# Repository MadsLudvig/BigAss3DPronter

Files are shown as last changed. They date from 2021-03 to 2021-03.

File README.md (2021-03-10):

# Industrial 3D Printer
*__Big 3D printer made with industrial parts from an injection molding machine__*

### Introduction

This is a 3D printer made with an extruder from an injection moulding machine and Motors and axis from several old ATM CNC robots. It will be using an material dryer and a mini vacuum conveyor for supplying the extruder with material. It will be build such that the extruder only moves on one axis because of its weight (approximately 50kg). The extruder will be moved on the x-axis and the bottom plate will be moved on the z- and y-axis. The software will be Marlin which is going to run on a Teensy 4.0. Then octoprint will be used as an Marlin host to control. Here octoprint will run on a Raspberry Pi 4.0 with an 15" industrial grade touch screen.

*__More information on the individual modules can be seen in the "Modules" folder__*

### Mechanical composition

Here as said before the extruder is going to be moved in the X-axis and the bottom plate is going to be moved in the Y- and Z-axis. This is seen in Figure 5 below:

3D-Printer-Axis

*Figure 5: Here is seen an example of how the axis will look*

Here it should be noted that although the axis placements are correct on the image. The way the axisses are moved are not. This image is just to show axis placement. The Z-axis is not moving the extruder it should here be moving the bottom plate instead. The reason why the extruder is placed on the x-axis is because of its sheer size and weight. Here it will be advantagous only to move it from side to side to minimize movement of mass. To make the x-axis move the weight of the extruder, the long axis of the ATM CNC robot is going to be used. This is because this has lots of already built-in support and can therefore support the extruder with ease. It also has place for motor mounting, gear and gearrack for moving the axis, and a cable carrier. This i going to be very advantageus for running the material supply line for the extruder, motor cables for x and w axisses, and heating element wires for extruder. Everything will then be mounted on a steel frame made out of welded steel beams. The material of the bottom plate is being researched, so the best material can be found. For now the material is aluminium, but that could also be replaced with borosilicate glass because of its hardness and temperature resistance

### Global Bill of Materials

| Name | Quantity | Link | Price (DKK) |
| :--- | :---: | :---: | :---: |
| Conradt mini vacuum conveyer | 1 | | 4000 |
| ILCE-QX1 Power adapter | 1 | [Link](https://www.subtel.dk/index.php?offerId=3978956963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) | 259 |
| 15" Touch screen | 1 | [Link](https://www.beetronics.dk/15-tommer-touchskaerm-metal-4-3) | 2699 |
| Cable | 1 | [Link](https://dk.rs-online.com/web/p/yy-kabel/1811780/) | 589 |
| Connector | 16 |  [Link](https://dk.rs-online.com/web/p/d-sub-stik/5443749/)  | 6.376 |
| Connector house | 16 | [Link](https://dk.rs-online.com/web/p/d-sub-bagkapper/5444039/) | 27.22 |
| Material dryer | 1 | | NaN |
| SN74LS640N | 6 | [Link](https://www.ti.com/store/ti/en/p/product/?p=SN74LS640N) | 9.54 |
| SN74ABT245BN | 6 | [Link](https://www.ti.com/store/ti/en/p/product/?p=SN74ABT245BN) | 4.52 |
| Aluminium bottom plate | 1 | | NaN |
| Heating elements bottom plate | 1 | | NaN |
| Steel frame | 1 | | NaN |
| Mounting adapter for servo motor to extruder | 1 | | NaN |

So here the price comes up to: 8169kr. DKK for now. Here it should be noted that this is not close to the final cost, since the mounting brackets, the steel frame, and the aluminium bottom plate will cost a lot.

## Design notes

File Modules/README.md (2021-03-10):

# Module Interfacing

### Module interfacing can be seen in the diagram below

*-- Insert diagram here --*

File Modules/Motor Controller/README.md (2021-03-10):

# Motor Controller
The motors are controlled by lenze servo controllers. All of the servo drives and the power management are already packed in a nice cabinet. This will be reused. Here the teensy will be sitting inside this cabinet. The model of the servo controllers is Lenze 9300. Here the X9 and X10 connectors will be used as seen here:

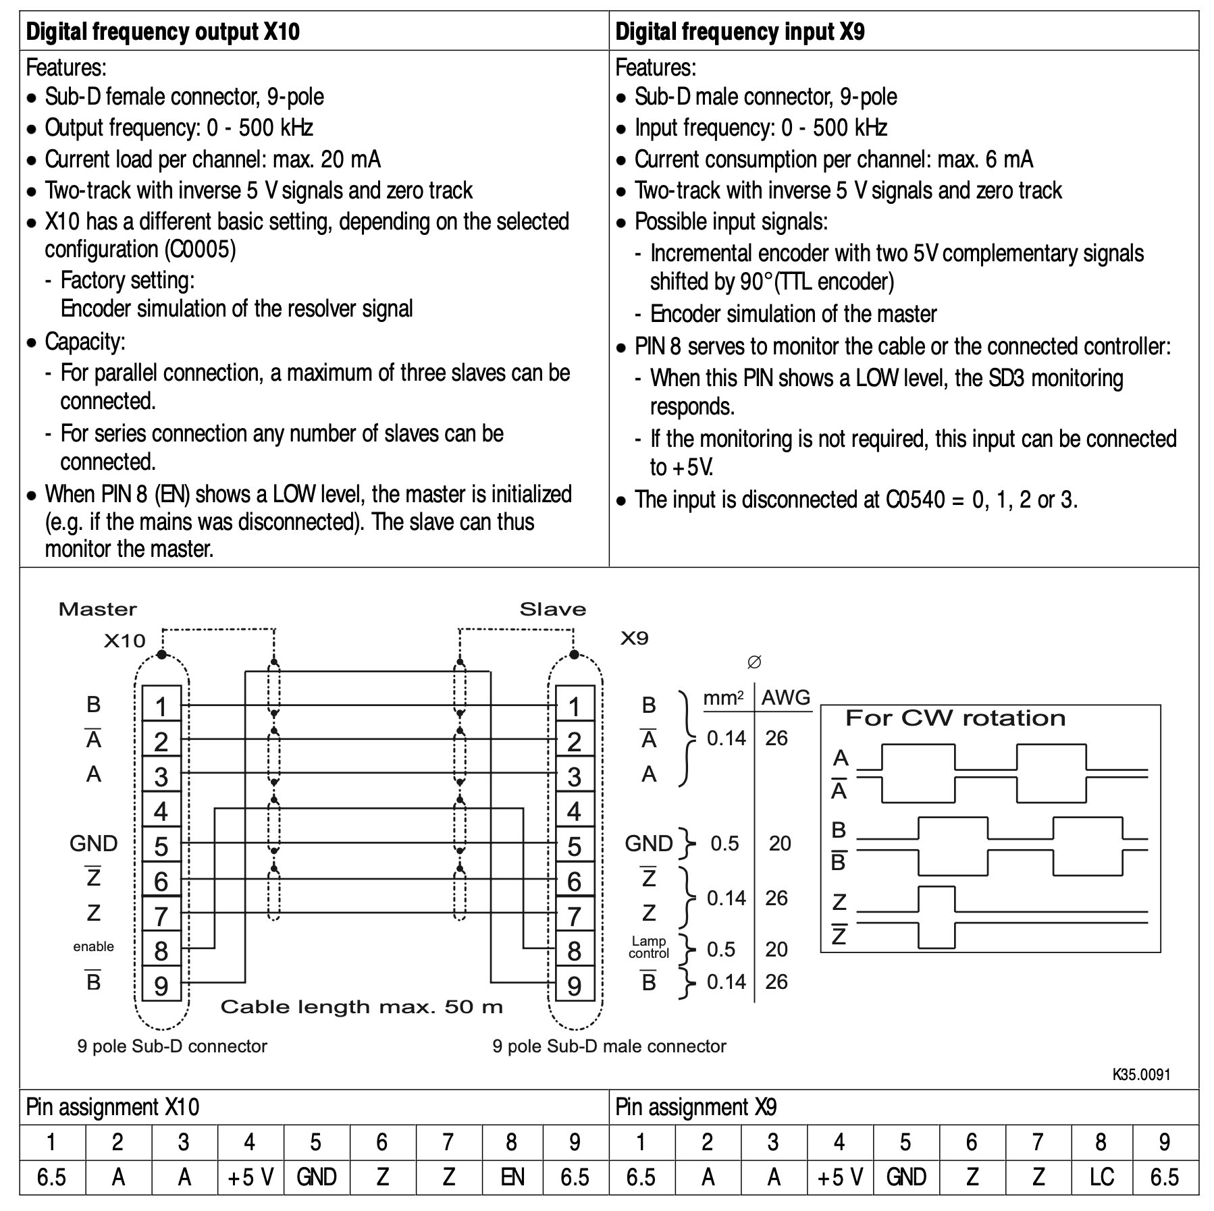
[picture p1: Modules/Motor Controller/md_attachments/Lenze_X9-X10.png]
Lenze X9-X10


*Figure 1: Page 47 of lenze 9300 servodrive manual*

*__Lenze manual:  [BA_9300_Register_control_EN.pdf](/md_attachments/BA_9300_Register_control_EN.pdf)__*

Here the X9 connector is digital frequency input. This input requires a TTL encoder signal. Then the servo drive will mimic this encoder signal. This way the drive can be controlled. So the Teensy 4.0 will input the Marlin stepper signals to this input. The plan is to have 4 outputs on the teensy that, so the X,Y,Z,W axisses can be controlled. Here the W axis is the motor that turns the extruder. Another nice feature this allows is that the servo drives can easily be daisy chained if multiple motors is needed per axis by connecting the X10 and X9. 

To make connecting the inputs to the Teensy 4.0, a circuitboard is going to be made with 4 d-sub connectors. Here is the current state of the board drawing and schematic:

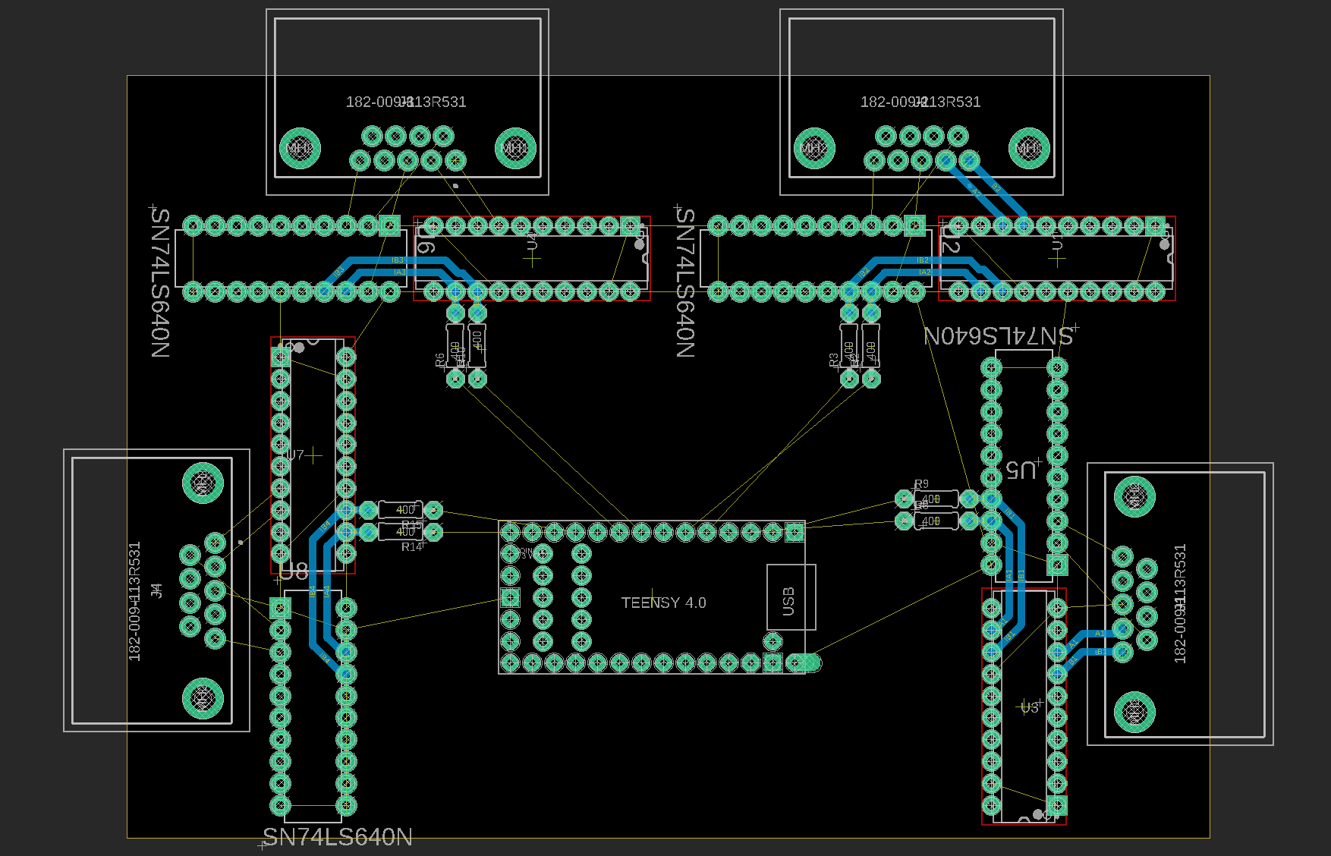
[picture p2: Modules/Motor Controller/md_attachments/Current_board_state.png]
Current board state


*Figure 2: Board*

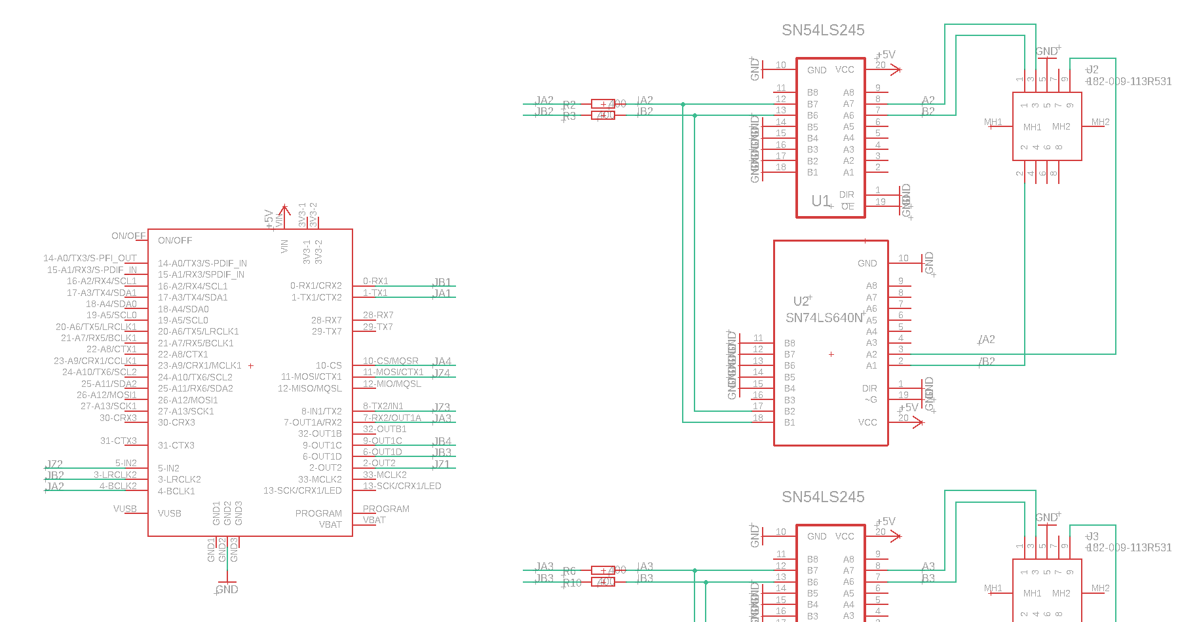
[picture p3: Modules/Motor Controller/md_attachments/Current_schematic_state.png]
Current schematic state


*Figure 3: Here is seen a piece of the schematic*

As seen in figure 2, non-inverting- and inverting bus-trancievers are used to unload the teensy's output GPIO pins. The reason the inverting bus-trancievers are used is because the input signal is differential as seen in figure 1. 

The reason why the stepper output of Marlin can be connected directly to the TTL encoder signal of the X9 input is because the signals are identical as seen by comparing Figure 1 and Figure 4 below:

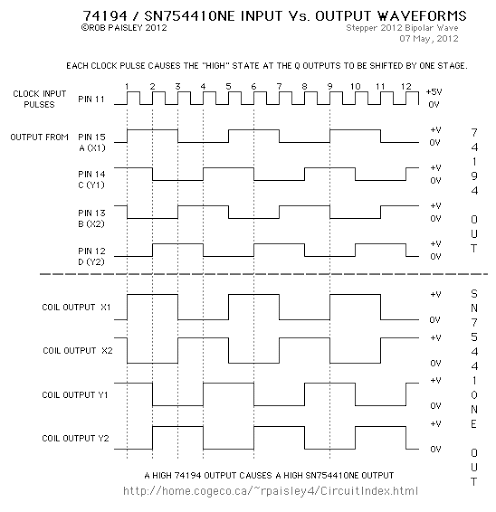
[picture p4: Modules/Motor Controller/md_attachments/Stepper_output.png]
Stepper output


*Figure 4: Here is seen the stepper output marlin*

Here it should be noted that the Z signal is not necessary to use, so it will not be used. The z signal just signifies when the encoder has turned one revolution. This will not be relevant though since all stepping amounts will be calibrated in marlin at last.

#### The cable between X9 and X10

As seen in figure 1 there are specific requirements for the specific leaders in the cable that is going to run between x9 and x10. Here there have been chosen a 9-conductor cable at 0.5mm2. The connectors are going to be female-female, so there have been chosen some 9-pin d-sub connectors. The links for the parts can be seen in the BoM

### Bill of Materials

| Name | Quantity | Link | Price(DKK) |
| :--- | :---: | :---: | :---: |
| Cable | 1 | [Link](https://dk.rs-online.com/web/p/yy-kabel/1811780/) | 589 |
| D-sub Connector | 16 |  [Link](https://dk.rs-online.com/web/p/d-sub-stik/5443749/)  | 6.376 |
| D-sub Connector house | 16 | [Link](https://dk.rs-online.com/web/p/d-sub-bagkapper/5444039/) | 27.22 |
| SN74LS640N | 6 | [Link](https://www.ti.com/store/ti/en/p/product/?p=SN74LS640N) | 9.54 |
| SN74ABT245BN | 6 | [Link](https://www.ti.com/store/ti/en/p/product/?p=SN74ABT245BN) | 4.52 |

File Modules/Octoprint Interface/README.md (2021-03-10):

# Octoprint with Raspberry Pi 4.0

Here as mentioned in the introduction Octoprint will be running on the raspberry pi. Here the raspberry pi will be connected to the Teensy via serial and a 15" touch screen will be connected to the Raspberry. The screen used will be this: [Link](https://www.beetronics.dk/15-tommer-touchskaerm-metal-4-3). The reason this HMI is used is because the ease of use that octoprint offers and future expansion of functionality is easy.

#### Camera in octoprint

Here a Sony QX1 will be mounted on the printer to monitor the printing process. The QX1 already outputs a mjpeg stream over its own network. So here the raspberry pi will be connected to the QX1's network. and input the stream into octoprint. In the future this functionality will be expanded to sending trigger commands to the QX1 to take pictures so octolapse can be integrated. Here a problem arises if the raspberry pi is to be connected to wifi and controlled remotely. To solve this problem either a WiFi dongle will be connected or the ethernet port on the raspberry will be used. A power adapter will here be used to power the qx1 constantly. This power adapter can be seen here: [Link](https://www.subtel.dk/index.php?offerId=3978956963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)

##### Camera commands so far to get live-view

For saving the liveview this command have been used on MacOS for now:

```bash
ffmpeg -i http://192.168.122.1:8080/liveview/liveviewstream -vcodec flv -qscale 1 -an output.flv
```

### Bill of Materials

| Name | Quantity | Link | Price (DKK) |
| :--- | :---: | :---: | :---: |
| ILCE-QX1 Power adapter | 1 | [Link](https://www.subtel.dk/index.php?offerId=3978956963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) | 259 |
| 15" Touch screen | 1 | [Link](https://www.beetronics.dk/15-tommer-touchskaerm-metal-4-3) | 2699 |

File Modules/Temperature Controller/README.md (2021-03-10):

# Temperature Controller

To control the temperature of the 6 heating bands on the extruder and the heating pads on the bottom plate, a PID controller will be made using a Raspberry Pi 3, 8 thermalcouple amplifiers and 8 solid-state relays. The outputs to the solid-state relays will be with PWM, so the temperature control is more precise. Then the Raspberry Pi 3 will run a webserver where temperature data can easily be requested and changes via POST and GET requests. This way the Raspberry Pi 4 running octoprint can request and change temperatures easily. The thermocouple amplifiers in question can be seen in the BoM. These have been chosen for their universitality of thermalcouple types and their i2c capability.

### Bill of Materials

| Name | Quantity | Link | Price(DKK) |
| :--- | :---: | :---: | :---: |
| Thermocouple Amplifier | 8 | [Link](https://www.digikey.dk/product-detail/da/adafruit-industries-llc/4101/1528-4101-ND/10245127?cur=USD&lang=da) | 97.6 |
| Solid-state relay | 8 | NaN | NaN |
| Raspberry Pi 3.0 | 1 | NaN | NaN |

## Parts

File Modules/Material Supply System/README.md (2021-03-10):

# Material Supply System

Here as said in the introduction a mini vacuum conveyer will be mounted on the extruder. Its material line, will then be run through the cable carrier and down to a material dryer which will be drying the material, so it has minimal moisture for fine prints. The mini vacuum conveyer in question is here the Conradt by Andertech as seen in this attachment: [CONRADT.pdf](md_attachments/CONRADT.pdf). The dryer in question is not found yet. The heating elements of the extruder will be powered by some sort of heat control elements. Preferably ones that can be controlled by software, so the temp can be controlled in the octoprint interface. But if this is out of the budget or simply not possible, conventional heat control elements will be used.

### Bill of Materials

| Name | Quantity | Link | Price (DKK) |
| :--- | :---: | :--: | :---: |
| Conradt mini vacuum conveyer  | 1 | | 4000 |
| Material dryer | 1 | | NaN |
| Heating elements bottom plate | 1 | | NaN |

.

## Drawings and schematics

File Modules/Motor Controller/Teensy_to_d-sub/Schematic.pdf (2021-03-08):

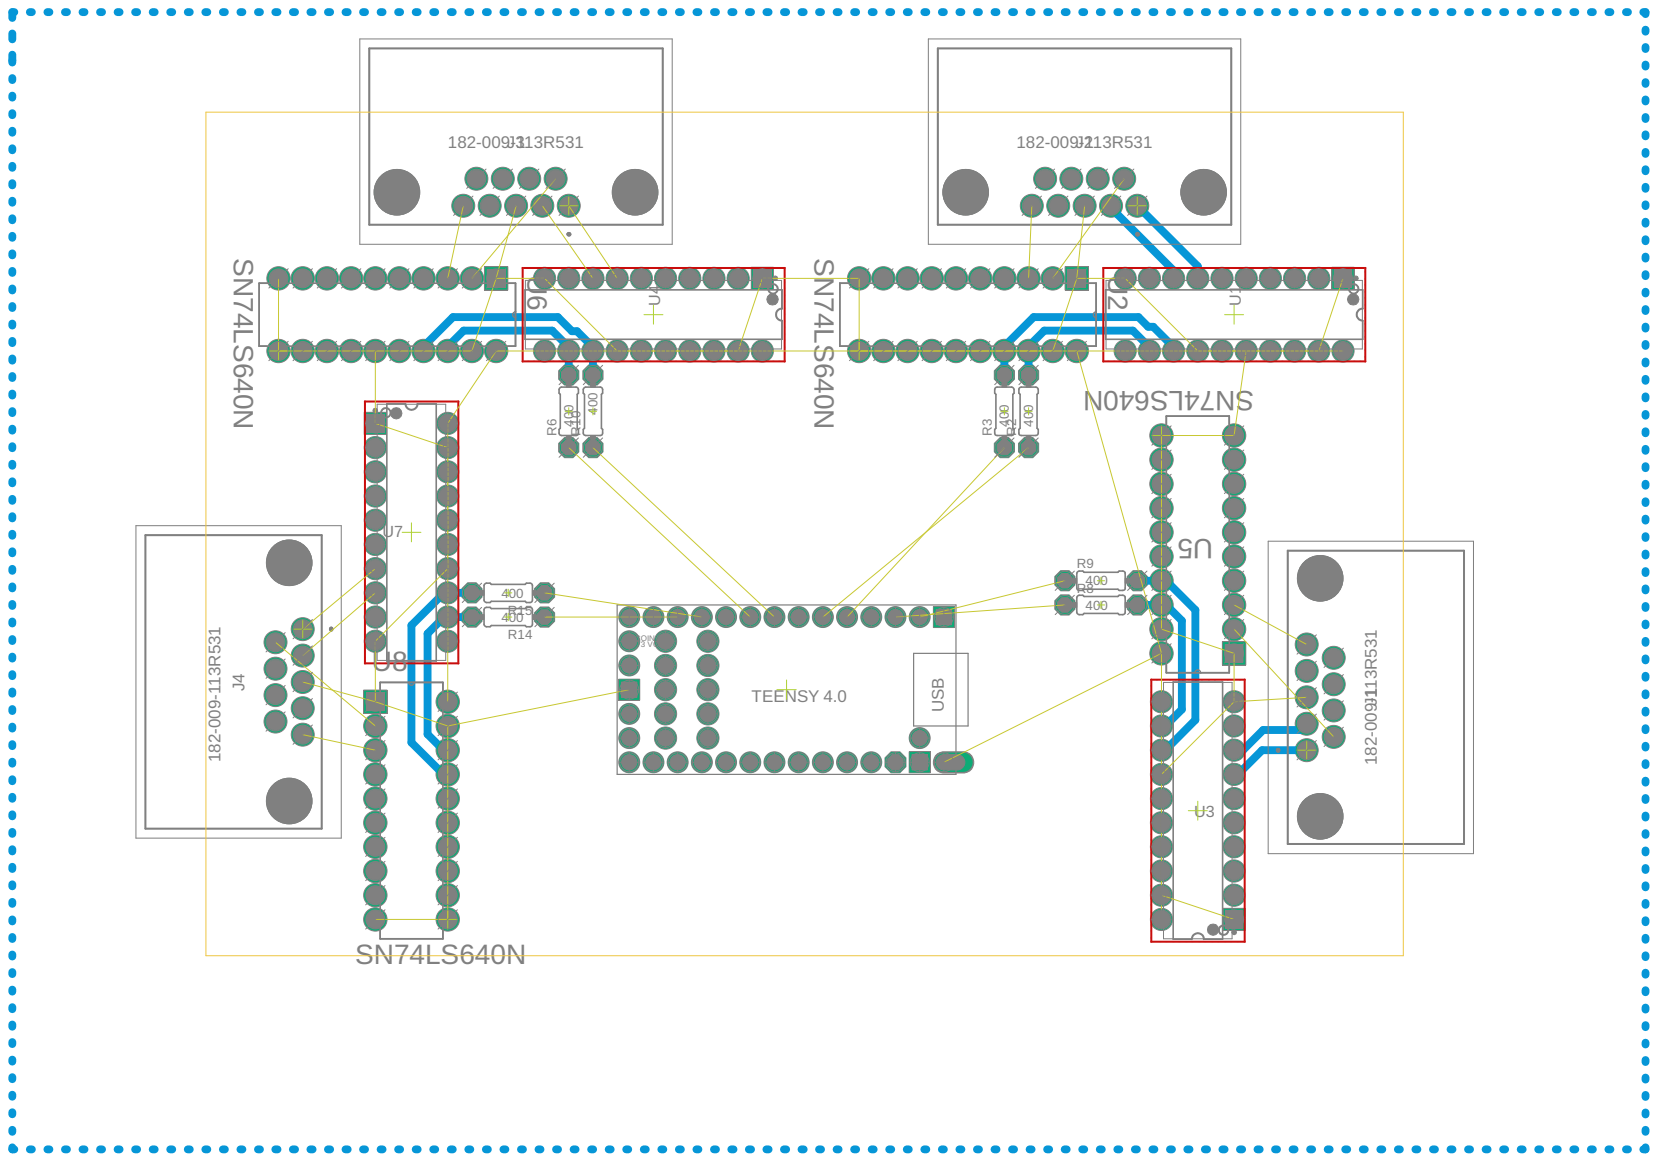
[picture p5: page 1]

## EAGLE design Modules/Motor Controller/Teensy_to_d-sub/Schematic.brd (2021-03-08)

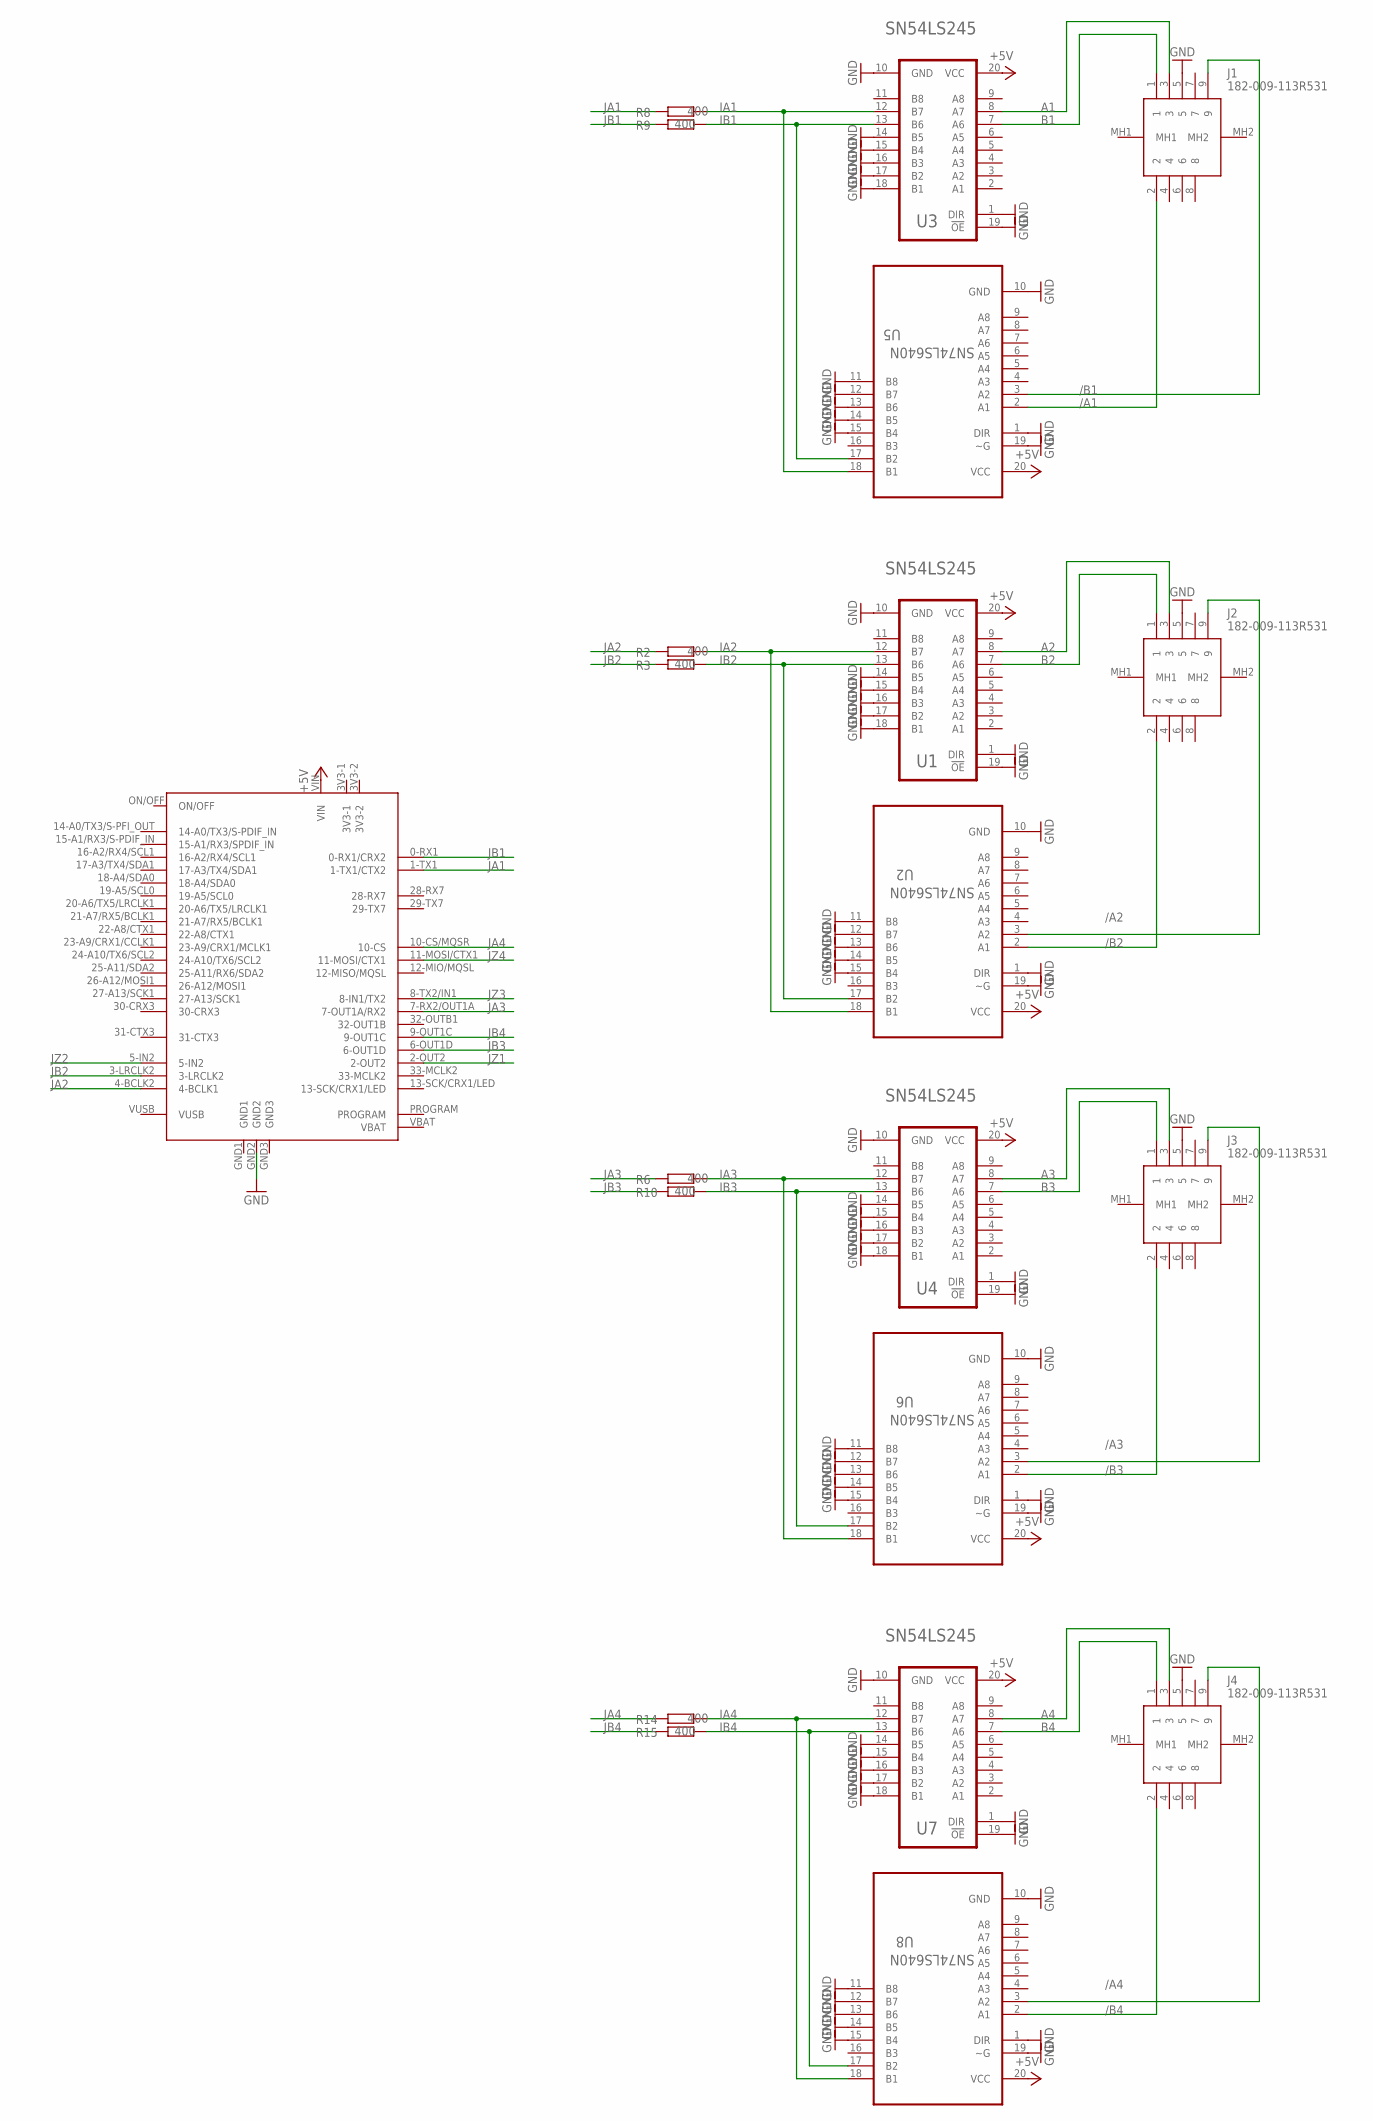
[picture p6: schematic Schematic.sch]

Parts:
J1, J2, J3, J4: 182-009-113R531; 182009113R531
R2, R3, R6, R8, R9, R10, R14, R15: 400; 0204/7
U1, U3, U4, U7: TEXAS_INSTRUMENTS_SN54LS245TEXAS_INSTRUMENTS_SN54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; TEXAS_INSTRUMENTS_SN54LS245_0
U2, U5, U6, U8: SN74LS640N; DIP254P762X508-20
U$1: TEENSY40

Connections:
+5V: U1.20 (VCC), U2.20 (VCC), U3.20 (VCC), U4.20 (VCC), U5.20 (VCC), U6.20 (VCC), U7.20 (VCC), U8.20 (VCC), U$1.VIN
/A1: J1.2, U5.2 (A1)
/A2: J2.2, U2.2 (A1)
/A3: J3.2, U6.2 (A1)
/A4: J4.2, U8.2 (A1)
/B1: J1.9, U5.3 (A2)
/B2: J2.9, U2.3 (A2)
/B3: J3.9, U6.3 (A2)
/B4: J4.9, U8.3 (A2)
A1: J1.3, U3.8 (A7)
A2: J2.3, U1.8 (A7)
A3: J3.3, U4.8 (A7)
A4: J4.3, U7.8 (A7)
B1: J1.1, U3.7 (A6)
B2: J2.1, U1.7 (A6)
B3: J3.1, U4.7 (A6)
B4: J4.1, U7.7 (A6)
GND: J1.5, J2.5, J3.5, J4.5, U1.1 (DIR), U1.10 (GND), U1.14 (B5), U1.15 (B4), U1.16 (B3), U1.17 (B2), U1.18 (B1), U1.19 (!OE!), U2.1 (DIR), U2.10 (GND), U2.11 (B8), U2.12 (B7), U2.13 (B6), U2.14 (B5), U2.15 (B4), U2.19 (~G), U3.1 (DIR), U3.10 (GND), U3.14 (B5), U3.15 (B4), U3.16 (B3), U3.17 (B2), U3.18 (B1), U3.19 (!OE!), U4.1 (DIR), U4.10 (GND), U4.14 (B5), U4.15 (B4), U4.16 (B3), U4.17 (B2), U4.18 (B1), U4.19 (!OE!), U5.1 (DIR), U5.10 (GND), U5.11 (B8), U5.12 (B7), U5.13 (B6), U5.14 (B5), U5.15 (B4), U5.19 (~G), U6.1 (DIR), U6.10 (GND), U6.11 (B8), U6.12 (B7), U6.13 (B6), U6.14 (B5), U6.15 (B4), U6.19 (~G), U7.1 (DIR), U7.10 (GND), U7.14 (B5), U7.15 (B4), U7.16 (B3), U7.17 (B2), U7.18 (B1), U7.19 (!OE!), U8.1 (DIR), U8.10 (GND), U8.11 (B8), U8.12 (B7), U8.13 (B6), U8.14 (B5), U8.15 (B4), U8.19 (~G), U$1.GND2
IA1: R8.2, U3.12 (B7), U5.18 (B1)
IA2: R2.2, U1.12 (B7), U2.18 (B1)
IA3: R6.2, U4.12 (B7), U6.18 (B1)
IA4: R14.2, U7.12 (B7), U8.18 (B1)
IB1: R9.2, U3.13 (B6), U5.17 (B2)
IB2: R3.2, U1.13 (B6), U2.17 (B2)
IB3: R10.2, U4.13 (B6), U6.17 (B2)
IB4: R15.2, U7.13 (B6), U8.17 (B2)
JA1: R8.1, U$1.1-TX1 (1-TX1/CTX2)
JA2: R2.1, U$1.4-BCLK2 (4-BCLK1)
JA3: R6.1, U$1.7-RX2/OUT1A (7-OUT1A/RX2)
JA4: R14.1, U$1.10-CS/MQSR (10-CS)
JB1: R9.1, U$1.0-RX1 (0-RX1/CRX2)
JB2: R3.1, U$1.3-LRCLK2
JB3: R10.1, U$1.6-OUT1D
JB4: R15.1, U$1.9-OUT1C
JZ1: U$1.2-OUT2
JZ2: U$1.5-IN2
JZ3: U$1.8-TX2/IN1 (8-IN1/TX2)
JZ4: U$1.11-MOSI/CTX1

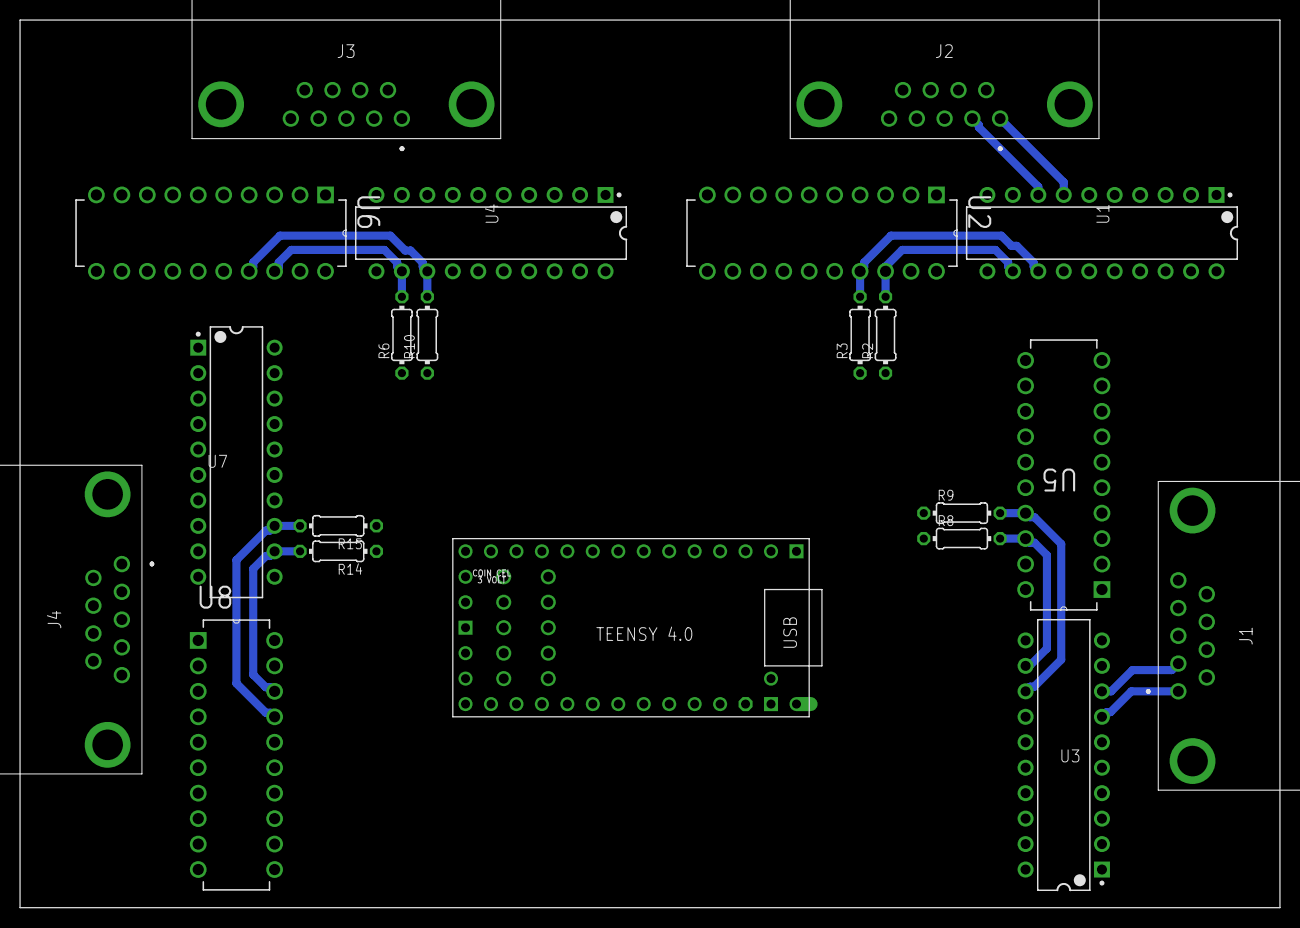
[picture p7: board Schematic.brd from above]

Board: 2 copper layers, 125.7 x 88.6 mm, 21 parts (0 on the bottom side), 34 nets.

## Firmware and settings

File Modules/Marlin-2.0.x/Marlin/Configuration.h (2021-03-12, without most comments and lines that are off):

#pragma once
#define CONFIGURATION_H_VERSION 020007
#define STRING_CONFIG_H_AUTHOR "(none, default config)" // Who made the changes.
#define SHOW_BOOTSCREEN
#define SERIAL_PORT 0
#define BAUDRATE 250000
  #define MOTHERBOARD BOARD_RAMPS_14_EFB
#define EXTRUDERS 1
#define DEFAULT_NOMINAL_FILAMENT_DIA 1.75
#define TEMP_SENSOR_0 1
#define TEMP_SENSOR_1 0
#define TEMP_SENSOR_2 0
#define TEMP_SENSOR_3 0
#define TEMP_SENSOR_4 0
#define TEMP_SENSOR_5 0
#define TEMP_SENSOR_6 0
#define TEMP_SENSOR_7 0
#define TEMP_SENSOR_BED 0
#define TEMP_SENSOR_PROBE 0
#define TEMP_SENSOR_CHAMBER 0
#define DUMMY_THERMISTOR_998_VALUE 25
#define DUMMY_THERMISTOR_999_VALUE 100
#define MAX_REDUNDANT_TEMP_SENSOR_DIFF 10
#define TEMP_RESIDENCY_TIME     10  // (seconds) Time to wait for hotend to "settle" in M109
#define TEMP_WINDOW              1  // (°C) Temperature proximity for the "temperature reached" timer
#define TEMP_HYSTERESIS          3  // (°C) Temperature proximity considered "close enough" to the target
#define TEMP_BED_RESIDENCY_TIME 10  // (seconds) Time to wait for bed to "settle" in M190
#define TEMP_BED_WINDOW          1  // (°C) Temperature proximity for the "temperature reached" timer
#define TEMP_BED_HYSTERESIS      3  // (°C) Temperature proximity considered "close enough" to the target
#define HEATER_0_MINTEMP   5
#define HEATER_1_MINTEMP   5
#define HEATER_2_MINTEMP   5
#define HEATER_3_MINTEMP   5
#define HEATER_4_MINTEMP   5
#define HEATER_5_MINTEMP   5
#define HEATER_6_MINTEMP   5
#define HEATER_7_MINTEMP   5
#define BED_MINTEMP        5
#define HEATER_0_MAXTEMP 275
#define HEATER_1_MAXTEMP 275
#define HEATER_2_MAXTEMP 275
#define HEATER_3_MAXTEMP 275
#define HEATER_4_MAXTEMP 275
#define HEATER_5_MAXTEMP 275
#define HEATER_6_MAXTEMP 275
#define HEATER_7_MAXTEMP 275
#define BED_MAXTEMP      150
#define PIDTEMP
#define BANG_MAX 255     // Limits current to nozzle while in bang-bang mode; 255=full current
#define PID_MAX BANG_MAX // Limits current to nozzle while PID is active (see PID_FUNCTIONAL_RANGE below); 255=full current
#define PID_K1 0.95      // Smoothing factor within any PID loop
    #define DEFAULT_Kp  22.20
    #define DEFAULT_Ki   1.08
    #define DEFAULT_Kd 114.00
#define MAX_BED_POWER 255 // limits duty cycle to bed; 255=full current
  #define PID_FUNCTIONAL_RANGE 10 // If the temperature difference between the target temperature and the actual temperature
#define PREVENT_COLD_EXTRUSION
#define EXTRUDE_MINTEMP 170
#define PREVENT_LENGTHY_EXTRUDE
#define EXTRUDE_MAXLENGTH 200
#define THERMAL_PROTECTION_HOTENDS // Enable thermal protection for all extruders
#define THERMAL_PROTECTION_BED     // Enable thermal protection for the heated bed
#define THERMAL_PROTECTION_CHAMBER // Enable thermal protection for the heated chamber
#define USE_XMIN_PLUG
#define USE_YMIN_PLUG
#define USE_ZMIN_PLUG
#define ENDSTOPPULLUPS
#define X_MIN_ENDSTOP_INVERTING false // Set to true to invert the logic of the endstop.
#define Y_MIN_ENDSTOP_INVERTING false // Set to true to invert the logic of the endstop.
#define Z_MIN_ENDSTOP_INVERTING false // Set to true to invert the logic of the endstop.
#define X_MAX_ENDSTOP_INVERTING false // Set to true to invert the logic of the endstop.
#define Y_MAX_ENDSTOP_INVERTING false // Set to true to invert the logic of the endstop.
#define Z_MAX_ENDSTOP_INVERTING false // Set to true to invert the logic of the endstop.
#define Z_MIN_PROBE_ENDSTOP_INVERTING false // Set to true to invert the logic of the probe.
#define DEFAULT_AXIS_STEPS_PER_UNIT   { 80, 80, 4000, 500 }
#define DEFAULT_MAX_FEEDRATE          { 300, 300, 5, 25 }
#define DEFAULT_MAX_ACCELERATION      { 3000, 3000, 100, 10000 }
#define DEFAULT_ACCELERATION          3000    // X, Y, Z and E acceleration for printing moves
#define DEFAULT_RETRACT_ACCELERATION  3000    // E acceleration for retracts
#define DEFAULT_TRAVEL_ACCELERATION   3000    // X, Y, Z acceleration for travel (non printing) moves
#define DEFAULT_EJERK    5.0  // May be used by Linear Advance
  #define JUNCTION_DEVIATION_MM 0.013 // (mm) Distance from real junction edge
  #define JD_HANDLE_SMALL_SEGMENTS    // Use curvature estimation instead of just the junction angle
#define Z_MIN_PROBE_USES_Z_MIN_ENDSTOP_PIN
#define NOZZLE_TO_PROBE_OFFSET { 10, 10, 0 }
#define PROBING_MARGIN 10
#define XY_PROBE_SPEED (133*60)
#define Z_PROBE_SPEED_FAST HOMING_FEEDRATE_Z
#define Z_PROBE_SPEED_SLOW (Z_PROBE_SPEED_FAST / 2)
#define Z_CLEARANCE_DEPLOY_PROBE   10 // Z Clearance for Deploy/Stow
#define Z_CLEARANCE_BETWEEN_PROBES  5 // Z Clearance between probe points
#define Z_CLEARANCE_MULTI_PROBE     5 // Z Clearance between multiple probes
#define Z_PROBE_LOW_POINT          -2 // Farthest distance below the trigger-point to go before stopping
#define Z_PROBE_OFFSET_RANGE_MIN -20
#define Z_PROBE_OFFSET_RANGE_MAX 20
#define X_ENABLE_ON 0
#define Y_ENABLE_ON 0
#define Z_ENABLE_ON 0
#define E_ENABLE_ON 0 // For all extruders
#define DISABLE_X false
#define DISABLE_Y false
#define DISABLE_Z false
#define DISABLE_E false             // Disable the extruder when not stepping
#define DISABLE_INACTIVE_EXTRUDER   // Keep only the active extruder enabled
#define INVERT_X_DIR false
#define INVERT_Y_DIR true
#define INVERT_Z_DIR false
#define INVERT_E0_DIR false
#define INVERT_E1_DIR false
#define INVERT_E2_DIR false
#define INVERT_E3_DIR false
#define INVERT_E4_DIR false
#define INVERT_E5_DIR false
#define INVERT_E6_DIR false
#define INVERT_E7_DIR false
#define X_HOME_DIR -1
#define Y_HOME_DIR -1
#define Z_HOME_DIR -1
#define X_BED_SIZE 200
#define Y_BED_SIZE 200
#define X_MIN_POS 0
#define Y_MIN_POS 0
#define Z_MIN_POS 0
#define X_MAX_POS X_BED_SIZE
#define Y_MAX_POS Y_BED_SIZE
#define Z_MAX_POS 200
#define MIN_SOFTWARE_ENDSTOPS
  #define MIN_SOFTWARE_ENDSTOP_X
  #define MIN_SOFTWARE_ENDSTOP_Y
  #define MIN_SOFTWARE_ENDSTOP_Z
#define MAX_SOFTWARE_ENDSTOPS
  #define MAX_SOFTWARE_ENDSTOP_X
  #define MAX_SOFTWARE_ENDSTOP_Y
  #define MAX_SOFTWARE_ENDSTOP_Z
#define HOMING_FEEDRATE_XY (50*60)
#define HOMING_FEEDRATE_Z  (4*60)
#define VALIDATE_HOMING_ENDSTOPS
#define EEPROM_CHITCHAT       // Give feedback on EEPROM commands. Disable to save PROGMEM.
#define EEPROM_BOOT_SILENT    // Keep M503 quiet and only give errors during first load
#define HOST_KEEPALIVE_FEATURE        // Disable this if your host doesn't like keepalive messages
#define DEFAULT_KEEPALIVE_INTERVAL 2  // Number of seconds between "busy" messages. Set with M113.
#define BUSY_WHILE_HEATING            // Some hosts require "busy" messages even during heating
#define PREHEAT_1_LABEL       "PLA"
#define PREHEAT_1_TEMP_HOTEND 180
#define PREHEAT_1_TEMP_BED     70
#define PREHEAT_1_FAN_SPEED     0 // Value from 0 to 255
#define PREHEAT_2_LABEL       "ABS"
#define PREHEAT_2_TEMP_HOTEND 240
#define PREHEAT_2_TEMP_BED    110
#define PREHEAT_2_FAN_SPEED     0 // Value from 0 to 255
#define PRINTJOB_TIMER_AUTOSTART
#define LCD_LANGUAGE en
#define DISPLAY_CHARSET_HD44780 JAPANESE
#define LCD_INFO_SCREEN_STYLE 0
#define SOFT_PWM_SCALE 0
#define SERVO_DELAY { 300 }

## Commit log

2021-03-08 Added Eagle files
    [Schematic.brd, Schematic.sch]
2021-03-10 Organised with modules folder
    [Schematic.brd, Schematic.sch]
2021-03-12 Added marlin firmware
    [Configuration.h, Configuration_adv.h]

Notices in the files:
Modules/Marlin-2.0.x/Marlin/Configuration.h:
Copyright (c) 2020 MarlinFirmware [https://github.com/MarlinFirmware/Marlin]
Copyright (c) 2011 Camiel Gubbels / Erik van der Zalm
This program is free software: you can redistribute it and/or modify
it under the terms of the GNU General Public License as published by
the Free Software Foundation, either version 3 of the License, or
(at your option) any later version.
